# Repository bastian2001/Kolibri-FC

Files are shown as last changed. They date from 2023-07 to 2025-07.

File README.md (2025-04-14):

# RP2350 Flight Controller for FPV

I wanted to have some fun designing my own flight controller in both hardware and software. [This project of mine](https://github.com/bastian2001/Hardware-DShot-on-RP2040) ([superseded](https://github.com/bastian2001/pico-bidir-dshot/)) served as a proof of concept (and mostly minimal example) that the RP2040 is capable of driving DShot through the PIO (Programmable IO) hardware.

The PCB is in its fifth testing revision, which includes (hardware features):

-   3-8S input voltage
-   5V 2.5A, 10V 2.5A buck converters
-   30.5mm stack mounting
-   BMI270
-   Analog character based OSD similar to Betaflight/iNav
-   SD card slot for blackbox, now with SDIO
-   Barometer (STM LPS22HB)
-   Gemini 2.4GHz ELRS receiver with 4 additional PWM outputs
-   Speaker driver up to VBat

Main software features:

-   Configurator
-   Acro and angle modes
-   altitude and position hold modes (working, but need to be tuned)
-   ELRS
-   GPS (UBlox) and Compass (HMC5883 + QMC5883L)
-   Bidirectional DShot 4800 (tested up to 1200)
-   Variable frequency beeper with WAV support
-   SD-Blackbox incl. viewer
-   Barometer (Goertek SPL06-001 + STM LPS22HB)

Future shit:

-   return to home and waypoint mission (incl. emergency switch)
-   3D camera dolly
-   trick trainer, that does a trick for you and displays in the OSD how good or bad you were at repeating that trick

Practically speaking, is there any reason to choose this over Betaflight or iNav? Likely not, but I want to have a challenge.

## Configurator screenshots

Home Page with a general preview of the quad's orientation, some status info and general controls
grafik

Blackbox viewer integrated into the configurator, you can record ELRS data, setpoints, rotation, attitude, PIDs, GPS, RPM, magnetometer and much more. Size is practically unlimited (SD card logging), but 1MB is about 10 seconds when logging practically everything. Integrated filtering to smooth noisy data, multiple graphs and multiple traces per graph, JSON converter for external analysis, pinch to zoom (touchscreen support). Don't mind the "Start Time" - it's wrong. The blackbox got some updates, which changed the interpretation of the timestamp.
grafik

Tasks viewer shows the execution duration and frequency of all the tasks to check they're running fast enough and to aid optimization of code (counting of frequency, max, min and average durations are not always done the same, so the results need to be checked against the code to see how each task is counted)
grafik

Receiver page shows status of the RX and each channel
grafik

Tuning is limited to basic PIDs and rates for now - filters have hardcoded cutoffs 😅
grafik

GPS + Mag page shows X/Y Y/Z and Z/X graphs of the magnetometer to check calibration and skew. Lower side shows data obtained by the GPS (no GPS fix right now, so time is off)
grafik

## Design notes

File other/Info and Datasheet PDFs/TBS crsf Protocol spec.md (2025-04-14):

Copied from https://github.com/tbs-fpv/tbs-crsf-spec/blob/main/crsf.md

CRSF V3 Protocol Specification © 2020 by TBS Avionics Co LTD is licensed under Creative Commons Attribution-ShareAlike 4.0 International

Unmodified, access date is April 14th 2025.

# CRSF Protocol

# Table of Contents

-   [CRSF Protocol](#crsf-protocol)
-   [Table of Contents](#table-of-contents)
-   [Features](#features)
-   [Purpose](#purpose)
-   [Acronyms](#acronyms)
-   [Hardware](#hardware)
    -   [Single-Wire Half-Duplex UART](#single-wire-half-duplex-uart)
    -   [Dual-Wire Full-Duplex UART](#dual-wire-full-duplex-uart)
    -   [Multi-master I2C (BST)](#multi-master-i2c-bst)
-   [Frame Construction](#frame-construction)
    -   [Structure](#structure)
    -   [Broadcast Frame](#broadcast-frame)
    -   [Extended Header Frame](#extended-header-frame)
    -   [Frame Details](#frame-details)
-   [Routing](#routing)
-   [CRC](#crc)
-   [Device Addresses](#device-addresses)
-   [Broadcast Frame Types](#broadcast-frame-types)
    -   [0x02 GPS](#0x02-gps)
    -   [0x03 GPS Time](#0x03-gps-time)
    -   [0x06 GPS Extended](#0x06-gps-extended)
    -   [0x07 Variometer Sensor](#0x07-variometer-sensor)
    -   [0x08 Battery Sensor](#0x08-battery-sensor)
    -   [0x09 Barometric Altitude & Vertical Speed](#0x09-barometric-altitude--vertical-speed)
    -   [0x0A Airspeed](#0x0a-airspeed)
    -   [0x0B Heartbeat](#0x0b-heartbeat)
    -   [0x0C RPM](#0x0C-rpm)
    -   [0x0D TEMP](#0x0D-temp)
    -   [0x0F Discontinued](#0x0f-discontinued)
    -   [0x10 VTX Telemetry](#0x10-vtx-telemetry)
    -   [0x14 Link Statistics](#0x14-link-statistics)
    -   [0x16 RC Channels Packed Payload](#0x16-rc-channels-packed-payload)
    -   [0x17 Subset RC Channels Packed](#0x17-subset-rc-channels-packed)
    -   [0x18 RC Channels Packed 11-bits (Unused)](#0x18-rc-channels-packed-11-bits-unused)
    -   [0x19 - 0x1B Reserved Crossfire](#0x19---0x1b-reserved-crossfire)
    -   [0x1C Link Statistics RX](#0x1c-link-statistics-rx)
    -   [0x1D Link Statistics TX](#0x1d-link-statistics-tx)
    -   [0x1E Attitude](#0x1e-attitude)
    -   [0x1F MAVLink FC](#0x1f-mavlink-fc)
    -   [0x21 Flight Mode](#0x21-flight-mode)
    -   [0x22 ESP_NOW Messages](#0x22-esp_now-messages)
    -   [0x27 Reserved](#0x27-reserved)
-   [Extended Frame Types](#extended-frame-types)
    -   [0x28 Parameter Ping Devices](#0x28-parameter-ping-devices)
    -   [0x29 Parameter Device Information](#0x29-parameter-device-information)
    -   [Chunks](#chunks)
    -   [0x2B Parameter Settings (Entry)](#0x2b-parameter-settings-entry)
        -   [Parameter Type Definitions & Hidden Bit](#parameter-type-definitions--hidden-bit)
        -   [OUT_OF_RANGE](#out_of_range)
        -   [UINT8, INT8, UINT16, INT16, UINT32, INT32](#uint8-int8-uint16-int16-uint32-int32)
        -   [FLOAT](#float)
        -   [TEXT_SELECTION](#text_selection)
        -   [STRING](#string)
        -   [FOLDER](#folder)
        -   [INFO](#info)
        -   [COMMAND](#command)
    -   [0x2C Parameter Settings (Read)](#0x2c-parameter-settings-read)
    -   [0x2D Parameter Value (Write)](#0x2d-parameter-value-write)
    -   [0x32 Direct Commands](#0x32-direct-commands)
        -   [0x32.0xFF Command ACK](#0x320xff-command-ack)
        -   [0x32.0x01 FC Commands](#0x320x01-fc-commands)
        -   [0x32.0x03 Bluetooth Command](#0x320x03-bluetooth-command)
        -   [0x32.0x05 OSD Commands](#0x320x05-osd-commands)
        -   [0x32.0x08 VTX Commands](#0x320x08-vtx-commands)
        -   [0x32.0x09 LED](#0x320x09-led)
        -   [0x32.0x0A General](#0x320x0a-general)
        -   [0x32.0x10 Crossfire](#0x320x10-crossfire)
        -   [0x32.0x12 Reserved](#0x320x12-reserved)
        -   [0x32.0x20 Flow Control Frame](#0x320x20-flow-control-frame)
        -   [0x32.0x22 Screen Command](#0x320x22-screen-command)
            -   [0x32.0x22.0x01 Pop-up Message Start](#0x320x220x01-pop-up-message-start)
            -   [0x32.0x22.0x02 Selection Return Value](#0x320x220x02-selection-return-value)
            -   [0x32.0x22.0x03 Reserved](#0x320x220x03-reserved)
            -   [0x32.0x22.0x04 Reserved](#0x320x220x04-reserved)
    -   [0x34 Logging](#0x34-logging)
    -   [0x36 Reserved](#0x36-reserved)
    -   [0x38 Reserved](#0x38-reserved)
    -   [0x3A - Remote Related Frames](#0x3a---remote-related-frames)
        -   [0x3A.0x01 - 0x3A.0x09 - Reserved](#0x3a0x01---0x3a0x09---reserved)
        -   [0x3A.0x10 Timing Correction (CRSF Shot)](#0x3a0x10-timing-correction-crsf-shot)
    -   [0x3C Game](#0x3c-game)
    -   [0x3E Reserved](#0x3e-reserved)
    -   [0x40 Reserved](#0x40-reserved)
    -   [0x78 - 0x79 KISSFC Reserved](#0x78---0x79-kissfc-reserved)
    -   [0x7A MSP Request / 0x7B Response](#0x7a-msp-request--0x7b-response)
    -   [0x7F ArduPilot Legacy Reserved](#0x7f-ardupilot-legacy-reserved)
    -   [0x80 ArduPilot Reserved Passthrough Frame](#0x80-ardupilot-reserved-passthrough-frame)
    -   [0x81, 0x82 mLRS Reserved](#0x81-0x82-mlrs-reserved)
    -   [0xAA CRSF MAVLink Envelope](#0xaa-crsf-mavlink-envelope)
    -   [0xAC CRSF MAVLink System Status Sensor](#0xac-crsf-mavlink-system-status-sensor)
-   [End of Document](#end-of-document)

# Features

-   Low latency high update rate for RC signals between RC - TX and RX - FC
-   Bidirectional communication
-   Share telemetry from flying platform to the RC
-   Edit configuration for direct connected devices and remotely connected devices (RC can configure FC or OSD over CRSF)
-   Share receiver serial number to TX, so it can be matched to model memory.

# Purpose

This document serves as a public "single source of truth", maintained by TBS, documenting the protocol. It serves as reference for implementation of CRSF-compatible devices, as well as allows developers not associated with TBS to voice requirements and suggest extensions to the existing protocols. It will further establish CRSF as the most widely implemented modern communication protocol for R/C devices.

# Acronyms

-   **CRSF** Binary frame-based protocol for radio-controlled devices. The subject of this document.
-   **RC** Remote Controller. The pilot control input device.
-   **TX** Transmitter (which is actually a transceiver). Usually a part (external or embedded as a radio module) of RC.
-   **RX** Receiver (which is also a transceiver). Might be as a separate device or embedded with FC or VTX.
-   **FC** Flight Controller.
-   **VTX** Video Transmitter.
-   **VRX** Video Receiver.

# Hardware

## Single-Wire Half-Duplex UART

This configuration is usually used between RC and TX. The RC acts as master in this case and TX responds with telemetry if it’s synchronized to the RC frames sent by the RC. The RC must send only one frame with pre-configured or negotiated frequency and must switch the line into the high-impedance mode and wait for a response from TX.

The UART by default runs at **400 kbaud 8N1** (inverted or non-inverted) at **3.3V** level, but it also supports 115.2 kbaud, and higher (1Mbaud, 2Mbaud) depending on hardware (see [0x70 CRSF Protocol Speed Proposal](#0x320x0a-general)). It is recommended that TX modules are configured to the same baud rate, or that they latch on to the correct baudrate automatically. The maximum frame-rate must be chosen depending on the baudrate for be able for RC and TX send frames with maximum length (64 bytes) in one frame.

## Dual-Wire Full-Duplex UART

This configuration is usually used on the flying platform side. Two devices are connected by regular UART connection. Only non-inverted (regular) UART is supported in this configuration. The UART runs by default at **416666 baud 8N1 at 3.0 to 3.3V level**, but baudrate can be negotiated to be higher to facilitate faster transmission for reducing latency.

## Multi-master I2C (BST)

(EOL) BST is a multi master I2C bus. It runs at 3.3V level at 100kHz using 7 bit addresses. Device addresses already contain the R/W bit. Which means the list is each device’s write address and read address is Device addresses + 1. Each device supporting BST should release SDA in any case to not block the bus. It’s recommended to monitor the heartbeat message and reset the interface if there is a timeout of 1.5s. It’s required to support general call frames which will be called broadcast frames within this document.

# Frame Construction

## Structure

The basic structure for each frame is the same. There is a range of Types with an extended header which will have the first few bytes of payload standardized. This is required to route frame across multiple devices for point to point communication. Each CRSF frame is not longer than **64 bytes** (including the Sync and CRC bytes)

## Broadcast Frame

```mermaid
flowchart LR
    id0[Sync byte] ~~~ id1[Frame Length] ~~~ Type ~~~ Payload ~~~ CRC
```

## Extended Header Frame

```mermaid
flowchart LR
    id0[Sync byte] ~~~ id1[Frame Length] ~~~ Type~~~ id2[Destination Address]  ~~~ id3[Origin Address]  ~~~ Payload ~~~ CRC
```

## Frame Details

-   **Sync byte** might be one of (so, receiving device should expect any of):
    -   Serial sync byte: **0xC8**;
    -   Broadcast device address: **0x00**;
    -   Device address (see addresses below).
-   **Frame length:** number of bytes in the frame excluding Sync byte and Frame Length (basically, entire frame size -2)
    -   **Broadcast Frame:** Type + Payload + CRC
    -   **Extended header frame:** Type + Destination address + Origin address + Payload + CRC
    -   Valid range is between 2 and 62. If this uint8 value is out of valid range the frame must be discarded.
-   **Type:** Frame type
-   **Endianness:** Big endian (MSB)

Frame size may be bigger than expected frame of given type. This should not be a reason to count the frame invalid. Frame receiver should just ignore extra fields. It's possible that frame sender supports a newer CRSF protocol version and sends some additional fields after known ones.

And vice-versa: if a frame has some optional fields, sometimes this fields might be set as empty fields (e.g. zero-length null-terminated string) but sometimes those fields might be absent and the frame size shortened. Don't try to read optional fields beyond frame payload.

# Routing

If a device has more than one CRSF port it’s required to forward all received frames to the other ports. CRSF works as a star network with fixed address tables on each node. It’s forbidden to use any loop connection as it would keep forwarding the same message endlessly.

# CRC

CRC includes Type and Payload of each frame (doesn't include sync byte and frame length).

CRC8 implementation with polynom = x7+ x6+ x4+ x2+ x0 (0xD5)

code example:

```cpp
unsigned char crc8tab[256] = {
    0x00, 0xD5, 0x7F, 0xAA, 0xFE, 0x2B, 0x81, 0x54, 0x29, 0xFC, 0x56, 0x83, 0xD7, 0x02, 0xA8, 0x7D,
    0x52, 0x87, 0x2D, 0xF8, 0xAC, 0x79, 0xD3, 0x06, 0x7B, 0xAE, 0x04, 0xD1, 0x85, 0x50, 0xFA, 0x2F,
    0xA4, 0x71, 0xDB, 0x0E, 0x5A, 0x8F, 0x25, 0xF0, 0x8D, 0x58, 0xF2, 0x27, 0x73, 0xA6, 0x0C, 0xD9,
    0xF6, 0x23, 0x89, 0x5C, 0x08, 0xDD, 0x77, 0xA2, 0xDF, 0x0A, 0xA0, 0x75, 0x21, 0xF4, 0x5E, 0x8B,
    0x9D, 0x48, 0xE2, 0x37, 0x63, 0xB6, 0x1C, 0xC9, 0xB4, 0x61, 0xCB, 0x1E, 0x4A, 0x9F, 0x35, 0xE0,
    0xCF, 0x1A, 0xB0, 0x65, 0x31, 0xE4, 0x4E, 0x9B, 0xE6, 0x33, 0x99, 0x4C, 0x18, 0xCD, 0x67, 0xB2,
    0x39, 0xEC, 0x46, 0x93, 0xC7, 0x12, 0xB8, 0x6D, 0x10, 0xC5, 0x6F, 0xBA, 0xEE, 0x3B, 0x91, 0x44,
    0x6B, 0xBE, 0x14, 0xC1, 0x95, 0x40, 0xEA, 0x3F, 0x42, 0x97, 0x3D, 0xE8, 0xBC, 0x69, 0xC3, 0x16,
    0xEF, 0x3A, 0x90, 0x45, 0x11, 0xC4, 0x6E, 0xBB, 0xC6, 0x13, 0xB9, 0x6C, 0x38, 0xED, 0x47, 0x92,
    0xBD, 0x68, 0xC2, 0x17, 0x43, 0x96, 0x3C, 0xE9, 0x94, 0x41, 0xEB, 0x3E, 0x6A, 0xBF, 0x15, 0xC0,
    0x4B, 0x9E, 0x34, 0xE1, 0xB5, 0x60, 0xCA, 0x1F, 0x62, 0xB7, 0x1D, 0xC8, 0x9C, 0x49, 0xE3, 0x36,
    0x19, 0xCC, 0x66, 0xB3, 0xE7, 0x32, 0x98, 0x4D, 0x30, 0xE5, 0x4F, 0x9A, 0xCE, 0x1B, 0xB1, 0x64,
    0x72, 0xA7, 0x0D, 0xD8, 0x8C, 0x59, 0xF3, 0x26, 0x5B, 0x8E, 0x24, 0xF1, 0xA5, 0x70, 0xDA, 0x0F,
    0x20, 0xF5, 0x5F, 0x8A, 0xDE, 0x0B, 0xA1, 0x74, 0x09, 0xDC, 0x76, 0xA3, 0xF7, 0x22, 0x88, 0x5D,
    0xD6, 0x03, 0xA9, 0x7C, 0x28, 0xFD, 0x57, 0x82, 0xFF, 0x2A, 0x80, 0x55, 0x01, 0xD4, 0x7E, 0xAB,
    0x84, 0x51, 0xFB, 0x2E, 0x7A, 0xAF, 0x05, 0xD0, 0xAD, 0x78, 0xD2, 0x07, 0x53, 0x86, 0x2C, 0xF9};

uint8_t crc8(const uint8_t * ptr, uint8_t len)
{
    uint8_t crc = 0;
    for (uint8_t i=0; i<len; i++)
        crc = crc8tab[crc ^ *ptr++];
    return crc;
}
```

# Device Addresses

-   **0x00** Broadcast address
-   **0x0E** Cloud
-   **0x10** USB Device
-   **0x12** Bluetooth Module/WiFi
-   **0x13** Wi-Fi receiver (mobile game/simulator)
-   **0x14** Video Receiver
-   _0x20-0x7F Dynamic address space for NAT_
-   **0x80** OSD / TBS CORE PNP PRO
-   **0x90** ESC 1
-   **0x91** ESC 2
-   **0x92** ESC 3
-   **0x93** ESC 4
-   **0x94** ESC 5
-   **0x95** ESC 6
-   **0x96** ESC 7
-   **0x97** ESC 8
-   _0x8A Reserved_
-   _0xB0 Crossfire reserved_
-   _0xB2 Crossfire reserved_
-   **0xC0** Voltage/ Current Sensor / PNP PRO digital current sensor
-   **0xC2** GPS / PNP PRO GPS
-   **0xC4** TBS Blackbox
-   **0xC8** Flight controller
-   _0xCA Reserved_
-   **0xCC** Race tag
-   **0xCE** VTX
-   **0xEA** Remote Control
-   **0xEC** R/C Receiver / Crossfire Rx
-   **0xEE** R/C Transmitter Module / Crossfire Tx
-   _0xF0 reserved_
-   _0xF2 reserved_

# Broadcast Frame Types

Frames with type lower than 0x27 are broadcast frames and have simple (short) header.

## 0x02 GPS

```cpp
    int32_t latitude;       // degree / 10`000`000
    int32_t longitude;      // degree / 10`000`000
    uint16_t groundspeed;   // km/h / 100
    uint16_t heading;       // degree / 100
    uint16_t altitude;      // meter - 1000m offset
    uint8_t satellites;     // # of sats in view
```

## 0x03 GPS Time

This frame is needed for synchronization with the ublox time pulse. The maximum offset of time is +/-10ms.

```cpp
    int16_t year;
    uint8_t month;
    uint8_t day;
    uint8_t hour;
    uint8_t minute;
    uint8_t second;
    uint16_t millisecond;
```

## 0x06 GPS Extended

```cpp
    uint8_t fix_type;       // Current GPS fix quality
    int16_t n_speed;        // Northward (north = positive) Speed [cm/sec]
    int16_t e_speed;        // Eastward (east = positive) Speed [cm/sec]
    int16_t v_speed;        // Vertical (up = positive) Speed [cm/sec]
    int16_t h_speed_acc;    // Horizontal Speed accuracy cm/sec
    int16_t track_acc;      // Heading accuracy in degrees scaled with 1e-1 degrees times 10)
    int16_t alt_ellipsoid;  // Meters Height above GPS Ellipsoid (not MSL)
    int16_t h_acc;          // horizontal accuracy in cm
    int16_t v_acc;          // vertical accuracy in cm
    uint8_t reserved;
    uint8_t hDOP;           // Horizontal dilution of precision,Dimensionless in nits of.1.
    uint8_t vDOP;           // vertical dilution of precision, Dimensionless in nits of .1.
```

## 0x07 Variometer Sensor

```cpp
    int16_t v_speed;        // Vertical speed cm/s
```

## 0x08 Battery Sensor

```cpp
    int16_t voltage;        // Voltage (LSB = 10 µV)
    int16_t current;        // Current (LSB = 10 µA)
    uint24_t capacity_used; // Capacity used (mAh)
    uint8_t remaining;      // Battery remaining (percent)
```

## 0x09 Barometric Altitude & Vertical Speed

These frame allows sending altitude and vertical speed in a bit-efficient way. It allows in 3 bytes combine dm-precision altitude with 32-km range and 3cm/s-precision vertical speed with 25m/s range.

```cpp
    uint16_t altitude_packed;       // Altitude above start (calibration) point
                                    // See description below.
    int8_t   vertical_speed_packed; // vertical speed. See description below.
```

Altitude value depends on MSB (bit 15):

-   MSB = 0: altitude is in decimeters - 10000dm offset (so 0 represents -1000m; 10000 represents 0m (starting altitude); 0x7fff represents 2276.7m);
-   MSB = 1: altitude is in meters. Without any offset.

altitude pack/unpack functions example:

```cpp
int32_t get_altitude_dm(uint16_t packed){
    return (packed & 0x8000) ? (packed & 0x7fff) * 10 : (packed - 10000);
}

// Due to OpenTX counts any 0xFFFF value as incorrect,
// the maximum sending value is limited to 0xFFFE (32766 meters)
//pack function example:
uint16_t get_altitude_packed (int32_t altitude_dm){
    enum
    {
        ALT_MIN_DM = 10000,                     //minimum altitude in dm
        ALT_THRESHOLD_DM = 0x8000 - ALT_MIN_DM, //altitude of precision
                                                // changing in dm
        ALT_MAX_DM = 0x7ffe * 10 - 5,           //maximum altitude in dm
    }

    if(altitude_dm < -ALT_MIN_DM)               //less than minimum altitude
        return 0;                               //minimum
    if(altitude_dm > ALT_MAX_DM)                //more than maximum
        return 0xfffe;                          //maximum
    if(altitude_dm < ALT_THRESHOLD_DM)          //dm-resolution range
        return altitude_dm + ALT_MIN_DM;
    return ((altitude_dm + 5) / 10) | 0x8000;   //meter-resolution range
}
```

vertical speed is represented in cm/s with logarithmic scale and (un)packed by functions:

```cpp
const int   Kl = 100;       // linearity constant;
const float Kr = .026;      // range constant;

int8_t  get_vertical_speed_packed (int16 vertical_speed_cm_s){
    return (int8_t)(log(abs(vertical_speed_cm_s)/Kl + 1)/Kr)
                                 * sign(vertical_speed_cm_s);
}

int16_t get_vertical_speed_cm_s (int8_t vertical_speed_packed){
    return exp(abs(vertical_speed_packed * Kr) - 1) * Kl
                           * sign(vertical_speed_packed);
}

```

Such constants give ±2500cm/s range and 3cm/s precision at low speeds and 70cm/s precision at speed about 25m/s;

## 0x0A Airspeed

```cpp
    uint16_t speed;             // Airspeed in 0.1 * km/h (hectometers/h)
```

## 0x0B Heartbeat

```cpp
    int16_t origin_address;             // Origin Device address
```

## 0x0C RPM

Frame type used to transmit RPM (revolutions per minute) telemetry data from the craft to the transmitter. This frame can be used to report motor or propeller RPM for monitoring performance or diagnostics.

```cpp
    uint8_t    rpm_source_id;  // Identifies the source of the RPM data (e.g., 0 = Motor 1, 1 = Motor 2, etc.)
    int24_t    rpm_value[];      // 1 - 19 RPM values with negative ones representing the motor spinning in reverse
```

## 0x0D TEMP

Frame type used to transmit temperature telemetry data from the vehicle to the transmitter. This frame can be used to report temperature readings from various sources on the vehicle, such as motors, ESCs, or the environment.

```cpp
    uint8_t     temp_source_id;     // Identifies the source of the temperature data (e.g., 0 = FC including all ESCs, 1 = Ambient, etc.)
    int16_t     temperature[];        // up to 20 temperature values in deci-degree (tenths of a degree) Celsius (e.g., 250 = 25.0°C, -50 = -5.0°C)
```

## 0x0F Discontinued

## 0x10 VTX Telemetry

```cpp
    uint8_t     origin_address;
    uint8_t     power_dBm;          // VTX power in dBm
    uint16_t    frequency_MHz;      // VTX frequency in MHz
    uint8_t     pit_mode:1;         // 0=Off, 1=On
    uint8_t     pitmode_control:2;  // 0=Off, 1=On, 2=Switch, 3=Failsafe
    uint8_t     pitmode_switch:4;   // 0=Ch5, 1=Ch5 Inv, … , 15=Ch12 Inv
```

## 0x14 Link Statistics

Uplink is the connection from the ground to the UAV and downlink the opposite direction

```cpp
    uint8_t     up_rssi_ant1;       // Uplink RSSI Antenna 1 (dBm * -1)
    uint8_t     up_rssi_ant2;       // Uplink RSSI Antenna 2 (dBm * -1)
    uint8_t     up_link_quality;    // Uplink Package success rate / Link quality (%)
    int8_t      up_snr;             // Uplink SNR (dB)
    uint8_t     active_antenna;     // number of currently best antenna
    uint8_t     rf_profile;         // enum {4fps = 0 , 50fps, 150fps}
    uint8_t     up_rf_power;        // enum {0mW = 0, 10mW, 25mW, 100mW,
                                    // 500mW, 1000mW, 2000mW, 250mW, 50mW}
    uint8_t     down_rssi;          // Downlink RSSI (dBm * -1)
    uint8_t     down_link_quality;  // Downlink Package success rate / Link quality (%)
    int8_t      down_snr;           // Downlink SNR (dB)
```

## 0x16 RC Channels Packed Payload

16 channels packed into 22 bytes. In case of a Failsafe, this frame will no longer be sent (when the failsafe type is set to "cut"). It is recommended to wait for 1 second before starting the FC failsafe routine.

```cpp
#define TICKS_TO_US(x)  ((x - 992) * 5 / 8 + 1500)
#define US_TO_TICKS(x)  ((x - 1500) * 8 / 5 + 992)

// Center (1500µs) = 992

struct
{
    int channel_01: 11;
    int channel_02: 11;
    int channel_03: 11;
    int channel_04: 11;
    int channel_05: 11;
    int channel_06: 11;
    int channel_07: 11;
    int channel_08: 11;
    int channel_09: 11;
    int channel_10: 11;
    int channel_11: 11;
    int channel_12: 11;
    int channel_13: 11;
    int channel_14: 11;
    int channel_15: 11;
    int channel_16: 11;
};
```

## 0x17 Subset RC Channels Packed

> [!WARNING]
> This frame is discouraged for implementation. Revision is in progress.

```cpp
// Calculation example to convert rc values to channel values
#define PACK_TX(x)          ((x - 3750) * 8 / 25 + 993)
#define UNPACK_RX(x, S)     (x * S + 988)
// S = 1.0 for 10-bit, S = 0.5 for 11-bit, S = 0.25 for 12-bit, S = 0.125 for 13-bit

struct PACKED
{
    uint8_t     starting_channel:5;             // which channel number is the first one in the frame
    uint8_t     res_configuration:2;            // configuration for the RC data resolution
                                                // (10 - 13 bits)
    uint8_t     digital_switch_flag:1;          // configuration bit for digital channel
    uint16_t    channel[]:resolution;           // variable amount of channels
                                                // (with variable resolution based on the
                                                // res_configuration)
                                                // based on the frame size
    uint16_t    digital_switch_channel[]:10;    // digital switch channel
};
```

## 0x18 RC Channels Packed 11-bits (Unused)

same as 0x16, but same conversion style as 0x17

## 0x19 - 0x1B Reserved Crossfire

## 0x1C Link Statistics RX

```cpp
    uint8_t rssi_db;        // RSSI (dBm * -1)
    uint8_t rssi_percent;   // RSSI in percent
    uint8_t link_quality;   // Package success rate / Link quality (%)
    int8_t  snr;            // SNR (dB)
    uint8_t rf_power_db;    // rf power in dBm
```

## 0x1D Link Statistics TX

```cpp
    uint8_t rssi_db;        // RSSI (dBm * -1)
    uint8_t rssi_percent;   // RSSI in percent
    uint8_t link_quality;   // Package success rate / Link quality (%)
    int8_t  snr;            // SNR (dB)
    uint8_t rf_power_db;    // rf power in dBm
    uint8_t fps;            // rf frames per second (fps / 10)
```

## 0x1E Attitude

> [!WARNING]
> Angle values must be in -180° +180° range!

```cpp
    int16_t pitch;  // Pitch angle (LSB = 100 µrad)
    int16_t roll;   // Roll angle  (LSB = 100 µrad)
    int16_t yaw;    // Yaw angle   (LSB = 100 µrad)
```

## 0x1F MAVLink FC

```cpp
    int16_t     airspeed;
    uint8_t     base_mode;      // vehicle mode flags, defined in MAV_MODE_FLAG enum
    uint32_t    custom_mode;    // autopilot-specific flags
    uint8_t     autopilot_type; // FC type; defined in MAV_AUTOPILOT enum
    uint8_t     firmware_type;  // vehicle type; defined in MAV_TYPE enum
```

**Official MAVLink Documentation:**

-   [MAV_MODE_FLAG enum](https://mavlink.io/en/messages/common.html#MAV_MODE_FLAG)
-   [MAV_AUTOPILOT enum](https://mavlink.io/en/messages/common.html#MAV_AUTOPILOT)
-   [MAV_TYPE enum](https://mavlink.io/en/messages/common.html#MAV_TYPE)

## 0x21 Flight Mode

```cpp
    char[]  Flight mode  // Null-terminated string
```

## 0x22 ESP_NOW Messages

```cpp
    uint8_t VAL1;           // Used for Seat Position of the Pilot
    uint8_t VAL2;           // Used for the Current Pilots Lap
    char    VAL3[15];       // 15 characters for the lap time current/split
    char    VAL4[15];       // 15 characters for the lap time current/split
    char    FREE_TEXT[20];  // Free text of 20 character at the bottom of the screen
```

## 0x27 Reserved

# Extended Frame Types

Frames with type 0x28 and higher (except explicitly mentioned) have extended header (with destination and origin).

## 0x28 Parameter Ping Devices

The host can ping a specific device (destination node address of device) or all devices (destination node address 0x00 Broadcast address) and they will answer with the [Parameter device information frame](#0x29-parameter-device-information). The frame has no payload.

## 0x29 Parameter Device Information

```cpp
    char[]      Device_name;        // Null-terminated string
    uint32_t    Serial_number;
    uint32_t    Hardware_ID;
    uint32_t    Firmware_ID;
    uint8_t     Parameters_total;   // Total amount of parameters
    uint8_t     Parameter_version_number;
```

## Chunks

Maximum CRSF frame size is 64 bytes (including sync byte and CRC). The host should always read ([0x2C Parameter settings (read)](#0x2c-parameter-settings-read)) chunk number 0 by default. If the read parameter ([0x2B Parameter settings (entry)](#0x2b-parameter-settings-entry)) fits the maximum size it will answer with chunks remaining 0 inside the parameter frame. Otherwise, it will send how many chunks are left to read.

**Example of Parameter settings frames (0x2B and 0x2C) chain:**

```mermaid
---
title: Example
---
sequenceDiagram

    Host->>Device: (0x2C) Request: Read Param 2, Chunk 0
    Device->>Host: (0x2B) Reply: Param 2, Chunks remaining : 2
    note over Host,Device: parameter is too big to fit 62 bytes.The device split<br/>it up in 3 chunks. First chunk is sent with this frame<br/>and 2 are remaining

    Host->>Device: (0x2C) Request: Read Param 2, Chunk 1
    Device->>Host: (0x2B) Reply: Param 2, Chunks remaining: 1
    note over Host,Device: as the device answered with a chunk size >0,<br/>the host keeps reading the same parameter<br/>and increases the chunk count

    Host->>Device: (0x2C) Request: Read Param 2, Chunk 2
    Device->>Host: (0x2B) Reply: Param 2, Chunks remaining: 0

    note over Host,Device: Host received last chunk so it can ready<br/>any other parameter starting over with chunk 0
    Host->>Device: (0x2C) Request: Read Param 3, Chunk 0
    Device->>Host: (0x2B) Reply: Param 3, Chunks remaining: 0
```

**Payload of chunk frames has the following structure:**

```cpp
uint8_t Parameter_number;                           // starting from 0
uint8_t Parameter_chunks_remaining;                 // Chunks remaining count
        Part of Parameter settings (entry) payload. // up to 56 bytes
```

## 0x2B Parameter Settings (Entry)

This is how a device (node address) can share a parameter to another device. See [Chunks](#chunks)

> [!NOTE]
> If Data_type_payload_chunk \<= 56 it can be sent in 1 frame, otherwise payload will be split into 2 or more frames.

```cpp
    uint8_t         Sync_byte;                  // 0xc8
    uint8_t         Frame_length;
    uint8_t         Frame_type;                 // 0x2b = Parameter settings (entry)
    uint8_t         Destination_address;        // 0xea = RC
    uint8_t         Origin_address;             // 0xee = TX
    uint8_t         Parameter_number;           // starting from 0
    uint8_t         Parameter_chunks_remaining; // Chunks remaining count
    {
        Data_type_payload_chunk;                // see payload for each type below
    }
    uint8_t         CRC_8;                      // Frame CRC (see CRC topic)
```

### Parameter Type Definitions & Hidden Bit

Parameter type is 8bit wide. The bit 7 indicates if the parameter is hidden (1 = hidden / 0 = visible). This gives the ability to dynamically show or hide parameters depending on other parameters. Bit 6-0 holds the type of parameter information (enum data_type).

```cpp
enum data_type
{
    UINT8           = 0,  // deprecated
    INT8            = 1,  // deprecated
    UINT16          = 2,  // deprecated
    INT16           = 3,  // deprecated
    UINT32          = 4,  // deprecated
    INT32           = 5,  // deprecated
    FLOAT           = 8,
    TEXT_SELECTION  = 9,
    STRING          = 10,
    FOLDER          = 11,
    INFO            = 12,
    COMMAND         = 13,
    OUT_OF_RANGE    = 127
}
```

### OUT_OF_RANGE

This type will be sent if a parameter number out of the device parameter range will be requested. It will be also sent as the last parameter to let the host know the end of the parameter list on a Parameters settings list (read request).

### UINT8, INT8, UINT16, INT16, UINT32, INT32

Suggested for deprecation. These are currently implemented via FLOAT, which is more general.

### FLOAT

Value, min, max and default are sent as an INT32. The decimal point value tells how many digits of the value are behind the decimal point. Step size is the recommended increment or decrement value to modify the value.

**Float payload**

```cpp
    uint8_t         Parent_folder;              // Parameter number of the parent folder,
                                                // 0 means root folder
    enum data_type  Data_type;                  // 0x08 = float
    char[]          Name;                       // Null-terminated string
    int32_t         Value;
    int32_t         Min;
    int32_t         Max;
    int32_t         Default;
    uint8_t         Decimal_point;
    int32_t         Step_size;
    char[]          Unit;                       // Null-terminated string
```

### TEXT_SELECTION

The value part of this entry is separated in two parts. First part is a char array with all possible values in text format. They are separated by a semicolon (;) and the array is null-terminated at the end. The second part is an uint8_t variable with the current value. The min, max and default value is represented as uint8_t number where a 0 represents the first text. To modify this parameter only the uint8_t value needs to be sent for the new value.

**Text selection payload**

```cpp
    uint8_t         Parent folder;              // Parameter number of the parent folder,
                                                // 0 means root folder
    enum data_type  Data type;                  // 0x09 = text selection
    char[]          Name;                       // Null-terminated string
    char[]          Options;                    // Null-terminated string, the string is
                                                // semicolon-delimited list of values
    uint8_t         Value;
    uint8_t         Min;
    uint8_t         Max;
    uint8_t         Default;
    char[]          Unit;                       // Null-terminated string
```

### STRING

This type is for text modification. Only the current text will be transmitted. There is no min, max and default entry sent for this type.

**String payload**

```cpp
    uint8_t         Parent_folder;              // Parameter number of the parent folder,
                                                // 0 means root folder
    enum data_type  Data_type;                  // 0x0a = string
    char[]          Name;                       // Null-terminated string
    char[]          Value;                      // Null-terminated string
    uint8_t         String_max_length;          // for string type only
```

### FOLDER

Folder is used to make a better structure of the parameters. Every parameter has a parent entry where the parameter can link to the parent folder. Additionally, the folder will provide a list of its children and append the folder name. The end of the list is marked with a 0xFF byte. The list will hold the parameter number of the children.

**Folder payload**

```cpp
    uint8_t         Parent_folder;              // Parameter number of the parent folder,
                                                // 0 means root folder
    enum data_type  Data_type;                  // 0x0b = folder
    char[]          Name;                       // Null-terminated string
    uint8_t[]       List_of_children;           // with 0xFF entry to mark the list end
```

### INFO

Value is a null terminated string. Same as STRING, except that INFO entry cannot be modified and doesn’t include maximum length.

**Info payload**

```cpp
    uint8_t         Parent_folder;              // Parameter number of the parent folder,
                                                // 0 means root folder
    enum data_type  Data_type;                  // 0x0c = info
    char[]          Name;                       // Null-terminated string
    char[]          Info;                       // Null-terminated string
```

### COMMAND

With the type command the host is able to run/execute a function on a device. This can be anything: link bind crossfire, calibrate gyro/acc, etc.

The device default state is READY. Once the host wants to execute the function it writes the parameter with status START. Depending on the function the device switches to PROGRESS, CONFIRMATION_NEEDED or READY.

When the device sends CONFIRMATION_NEEDED the host will show a confirmation box with “confirm” or “cancel” selection. If the user selects one the selection will be transmitted to the device and the function continues to execute. With the field Info the device can send additional information to the host.

If the host sends status POLL, it will force the device to send an updated status of the 0x2B Parameter settings (entry).

**Command payload**

```cpp
struct
{
    uint8_t         Parent_folder;  // Parameter number of the parent folder, 0 means root folder
    enum data_type  Data_type;      // 0x0d = command
    char[]          Name;           // Null-terminated string
    enum cmd_status Status;         // uint8_t
    uint8_t         Timeout;        // ms * 100
    char[]          Info;           // Null-terminated string
}

enum cmd_status
{
    READY               = 0, //--> feedback
    START               = 1, //<-- input
    PROGRESS            = 2, //--> feedback
    CONFIRMATION_NEEDED = 3, //--> feedback
    CONFIRM             = 4, //<-- input
    CANCEL              = 5, //<-- input
    POLL                = 6  //<-- input
}
```

**Command chain example**

```mermaid
sequenceDiagram

    Host->>Device: Read parameter (0x2C)
    Device->>Host: Send: COMMAND, Name = Bind, Status = READY, Info = NULL (0x2B)
    Host->>Device: Write: Status = START (0x2D)
    Device->>Host: Send Parameter: COMMAND, Name = Bind, Status = PROGRESS, Info = Binding (0x2B)

    Host->>Device: (optional) Status = POLL (0x2D)
    note over Host: it’s a must to send POLL from host if we wanna get the <br/>latest parameter info.For example: while getting parameter “bind”<br/>from TX (0xEE) is a must,otherwise we don’t know the RX firmware<br/>updating info
    Host->>Device: (optional) Status = POLL (0x2D)
    Host->>Device: (optional) Status = POLL (0x2D)

    note over Device: Device completed bind process
    Device->>Host: Send Parameter: COMMAND, Name = Bind, Status = READY, Info = OK (0x2B)
```

## 0x2C Parameter Settings (Read)

Request a specific parameter. This command is for re-request a parameter/chunk that didn’t make it through the link.

```cpp
    uint8_t Parameter_number;
    uint8_t Parameter_chunk_number; // Chunk number to request, starts with 0
```

## 0x2D Parameter Value (Write)

This command is for override a parameter. The destination node will answer with a [0x2B Parameter Settings (Entry)](#0x2b-parameter-settings-entry) frame sent to the origin node address for verification.

```cpp
    uint8_t Parameter_number;
            Data;               // size depending on data type
```

> [!NOTE]
> Size depending on [data type](#parameter-type-definitions-and-hidden-bit), otherwise this entry
> is not sent, f.e.:
>
> -   for TEXT_SELECTION - size 1;
> -   for FLOAT - size 4.

## 0x32 Direct Commands

Command frame

```cpp
    uint8_t     Command_ID;
    uint8_t[]   Payload;        // depending on Command ID
    uint8_t     Command_CRC8;   // 8 bit CRC POLYNOM = 0xBA
```

Command frame is protected by additional CRC at the end of its payload. The CRC includes frame type (byte 0x32), Destination, Origin, Command ID and Payload of each Command Frame.

Command_CRC8 implementation with polynom = x7+ x5+ x4+ x3+ x1 (0xBA)

> [!NOTE]
> The polynom is different from the main CRSF frame CRC.

> [!NOTE]
> Command CRC doesn't exclude CRC at the end of each CRSF frame. You will also need to include CRC at the end for the full frame

```cpp
unsigned char command_crc8tab[256] = {
    0x00, 0xBA, 0xCE, 0x74, 0x26, 0x9C, 0xE8, 0x52, 0x4C, 0xF6, 0x82, 0x38, 0x6A, 0xD0, 0xA4, 0x1E,
    0x98, 0x22, 0x56, 0xEC, 0xBE, 0x04, 0x70, 0xCA, 0xD4, 0x6E, 0x1A, 0xA0, 0xF2, 0x48, 0x3C, 0x86,
    0x8A, 0x30, 0x44, 0xFE, 0xAC, 0x16, 0x62, 0xD8, 0xC6, 0x7C, 0x08, 0xB2, 0xE0, 0x5A, 0x2E, 0x94,
    0x12, 0xA8, 0xDC, 0x66, 0x34, 0x8E, 0xFA, 0x40, 0x5E, 0xE4, 0x90, 0x2A, 0x78, 0xC2, 0xB6, 0x0C,
    0xAE, 0x14, 0x60, 0xDA, 0x88, 0x32, 0x46, 0xFC, 0xE2, 0x58, 0x2C, 0x96, 0xC4, 0x7E, 0x0A, 0xB0,
    0x36, 0x8C, 0xF8, 0x42, 0x10, 0xAA, 0xDE, 0x64, 0x7A, 0xC0, 0xB4, 0x0E, 0x5C, 0xE6, 0x92, 0x28,
    0x24, 0x9E, 0xEA, 0x50, 0x02, 0xB8, 0xCC, 0x76, 0x68, 0xD2, 0xA6, 0x1C, 0x4E, 0xF4, 0x80, 0x3A,
    0xBC, 0x06, 0x72, 0xC8, 0x9A, 0x20, 0x54, 0xEE, 0xF0, 0x4A, 0x3E, 0x84, 0xD6, 0x6C, 0x18, 0xA2,
    0xE6, 0x5C, 0x28, 0x92, 0xC0, 0x7A, 0x0E, 0xB4, 0xAA, 0x10, 0x64, 0xDE, 0x8C, 0x36, 0x42, 0xF8,
    0x7E, 0xC4, 0xB0, 0x0A, 0x58, 0xE2, 0x96, 0x2C, 0x32, 0x88, 0xFC, 0x46, 0x14, 0xAE, 0xDA, 0x60,
    0x6C, 0xD6, 0xA2, 0x18, 0x4A, 0xF0, 0x84, 0x3E, 0x20, 0x9A, 0xEE, 0x54, 0x06, 0xBC, 0xC8, 0x72,
    0xF4, 0x4E, 0x3A, 0x80, 0xD2, 0x68, 0x1C, 0xA6, 0xB8, 0x02, 0x76, 0xCC, 0x9E, 0x24, 0x50, 0xEA,
    0x48, 0xF2, 0x86, 0x3C, 0x6E, 0xD4, 0xA0, 0x1A, 0x04, 0xBE, 0xCA, 0x70, 0x22, 0x98, 0xEC, 0x56,
    0xD0, 0x6A, 0x1E, 0xA4, 0xF6, 0x4C, 0x38, 0x82, 0x9C, 0x26, 0x52, 0xE8, 0xBA, 0x00, 0x74, 0xCE,
    0xC2, 0x78, 0x0C, 0xB6, 0xE4, 0x5E, 0x2A, 0x90, 0x8E, 0x34, 0x40, 0xFA, 0xA8, 0x12, 0x66, 0xDC,
    0x5A, 0xE0, 0x94, 0x2E, 0x7C, 0xC6, 0xB2, 0x08, 0x16, 0xAC, 0xD8, 0x62, 0x30, 0x8A, 0xFE, 0x44};
```

### 0x32.0xFF Command ACK

```cpp
    uint8_t Command_ID;;
    uint8_t SubCommand_ID;
    uint8_t Action;
        // 1 mean target already take action
        // 0 mean not a correct command or no function on that command yet
    uint8_t[] or char[] Information; // null terminated string
```

### 0x32.0x01 FC Commands

```cpp
- 0x01 Force Disarm
- 0x02 Scale Channel
```

### 0x32.0x03 Bluetooth Command

```cpp
- 0x01 Reset
- 0x02 Enable
  - uint8_t Enable (0 = disable, 1 = enable)
- 0x64 Echo
```

### 0x32.0x05 OSD Commands

```cpp
- 0x01 Send Buttons:
  - uint8_t Buttons bitwise (Bit 7=Enter, 6=Up, 5=Down, 4=Left, 3=Right)
```

### 0x32.0x08 VTX Commands

```cpp
- 0x01 DISCONTINUED VTX Change Channel
  - EVO, PRO32 HV, PRO32 NANO still support this.
- 0x02 Set frequency
  - uint16_t Frequency (5000 - 6000 MHz)
- 0x03 DISCONTINUED VTX Change Power (moved to 0x08)
- 0x04 Enable PitMode on power up
  - uint8_t PitMode:1 enum (0 = OFF, 1 = ON)
  - uint8_t pitmode_control:2; (0=Off, 1=On, 2=Arm, 3=Failsafe)
  - uint8_t pitmode_switch:4; (0=Ch5, 1=Ch5 Inv, … , 15=Ch12 Inv)
- 0x05 Power up from PitMode (bare command)
- 0x06 Set Dynamic Power (15/05/2020 in EVO, PRO32 HV, PRO32 NANO)
    NOTE: Needs to be sent at 1Hz. If not received for 3s the VTX
          will revert to “0x08 Set Power” power setting
  - uint8_t Power (dBm) (0dBm can be considered as PitMode Power)
- 0x08 Set Power
  - uint8_t Power (dBm) (0dBm can be considered as PitMode Power)
```

### 0x32.0x09 LED

```cpp
- 0x01 Set to default (revert to target specific settings)
- 0x02 Override LED color (packed)
  - 9 bits H (0-359°)
  - 7 bits S (0-100%)
  - 8 bits V (0-100%)
- 0x03 Override pulse (packed)
  - uint16 duration (milliseconds from start color to stop color)
  - 9 bits H_Start (0-359°)
  - 7 bits S_Start (0-100%)
  - 8 bits V_Start (0-100%)
  - 9 bits H_Stop (0-359°)
  - 7 bits S_Stop (0-100%)
  - 8 bits V_Stop (0-100%)
- 0x04 Override blink (packed)
  - uint16 Interval
  - 9 bits H_Start (0-359°)
  - 7 bits S_Start (0-100%)
  - 8 bits V_Start (0-100%)
  - 9 bits H_Stop (0-359°)
  - 7 bits S_Stop (0-100%)
  - 8 bits V_Stop (0-100%)
- 0x05 Override shift (packed)
  - uint16 Interval
  - 9 bits H (0-359°)
  - 7 bits S (0-100%)
  - 8 bits V (0-100%)
```

### 0x32.0x0A General

```cpp
- 0x04 - 0x61 reserved
- 0x70 CRSF Protocol Speed Proposal
  - uint8_t port_id
  - uint32  proposed_baudrate
- 0x71 CRSF Protocol Speed Proposal Response
  - uint8_t port_id
  - bool    response // (1 = accepted / 0 = rejected)
```

### 0x32.0x10 Crossfire

```cpp
- 0x01 Set receiver in bind mode
- 0x02 Cancel bind mode
- 0x03 Set bind ID
- 0x05 Model selection (command to select model/receiver)
  - uint8_t Model Number
- 0x06 Current model selection (query frame of current selection)
- 0x07 Reply current model selection (reply frame of current selection)
  - uint8_t Model Number
- 0x08 reserved
- 0x09 reserved
```

### 0x32.0x12 Reserved

### 0x32.0x20 Flow Control Frame

A device can limit data rate or subscribe to a specific frame.

```cpp
- 0x01 Subscribe
  - uint8_t  Frame type
  - uint16_t Max interval time // ms
- 0x02 Unsubscribe
  - uint8_t  Frame type
```

### 0x32.0x22 Screen Command

For all device which has LCD Screen

#### 0x32.0x22.0x01 Pop-up Message Start

```cpp
    char[]  Header;                 // Null terminated string
    char[]  Info message;           // Null terminated string
    uint8_t Max_timeout_interval;   // Time in seconds
    bool    Close_button_option;
    struct                          // optional field. If its first byte is null
                                    // (selectionText is empty)
                                    // then it's only 1-byte (null) long.
    {
        char[]  selectionText;      // Null-terminated string. If empty,
                                    // then other fields don't exist.
        uint8_t value;
        uint8_t minValue;
        uint8_t maxValue;
        uint8_t defaultValue;
        char[]  unit;               // Null terminated string of measurement unit
    }       add_data;               // additional data to show (e.g. percentage).
    char[]  possible_values;        // optional field. char array with all possible response
                                    // values in text format,
                                    // they are separated by a semicolon (;) and the array
                                    // is null-terminated.
```

> [!NOTE]
> optional fields might either start with null or not even fit in the frame. Analyze frame size and don't read optional fields beyond frame payload.

#### 0x32.0x22.0x02 Selection Return Value

```cpp
    uint8_t value;
    bool    response;   // true(Process)/false(Cancel)
```

#### 0x32.0x22.0x03 Reserved

#### 0x32.0x22.0x04 Reserved

## 0x34 Logging

this frame has simple (short) header. Used for degug purpose only.

```cpp
    uint16_t logtype;
    uint32_t timestamp;
    uint32_t para1;

    ...
    uint32_t paraN;
```

## 0x36 Reserved

## 0x38 Reserved

## 0x3A - Remote Related Frames

### 0x3A.0x01 - 0x3A.0x09 - Reserved

### 0x3A.0x10 Timing Correction (CRSF Shot)

aka “RC-sync”; aka “timing correction frame” (in EdgeTX).

```cpp
    uint32_t    update_interval;    // LSB = 100ns
    int32       offset;             // LSB = 100ns, positive values = data came too early,
                                    // negative = late.
```

Despite that the values are in 100ns resolution, at least in EdgeTX it’s rounded to 1µs resolution 16-bit values right on arriving.

## 0x3C Game

```cpp
- 0x01 Add points
  - int16 amount of points
- 0x02 Command code
  - uint16 code
```

## 0x3E Reserved

## 0x40 Reserved

## 0x78 - 0x79 KISSFC Reserved

## 0x7A MSP Request / 0x7B Response

**0x7A**

-   CRSF frame which wraps MSP request **(‘$M\<’ or ‘$X\<’)**
-   Supported by Betaflight devices
-   Supported devices will respond with 0x7B

**0x7B**

-   CRSF frame which wraps MSP response **(‘$M>’,’$X>’,‘$M!’,’$X!’)**
-   Supported by Betaflight devices
-   Supported device will send this frame in response of MSP_Request (0x7A)

MSP frame over CRSF Payload packing:

-   MSP frame is stripped from header ($ + M/X + [/]/!) and CRC
-   Resulted MSP-body might be divided in chunks if it doesn't fit in one CRSF-frame.
-   A ‘Status’ byte is put before MSP-body in each CRSF-frame.
-   Status byte consists of three parts:
    -   bits 0-3 represent cyclic sequence number of the CRSF frame;
    -   bit 4 checks if current MSP chunk is the beginning (or only) of a new frame (1 if true);
    -   bits 5-6 represent the version number of MSP protocol (1 or 2 currently);
    -   bit 7 represents an error (for response only).
-   Chunk size of the MSP-body is calculated from size of CRSF frame. But size of the MSP-body must be parsed from the MSP-body itself (with respect to MSP version and Jumbo-frame).
-   The last/only CRSF-frame might be longer than needed. In such a case, the extra bytes must be ignored.
-   Maximum chunk size is defined by maximum length of CRSF frame 64 bytes, therefore, maximum MSP-chunk length is **57** bytes. Minimum chunk length might by anything, but the first chunk must consist of size and function ID (i.e., 5 bytes for MSPv2).
-   CRC of the MSP frame is not sent because it’s already protected by CRC of CRSF. If MSP CRC is needed, it should be calculated at the receiving point.
-   MSP-response must be sent to the origin of the MSP-request. It means that _[destination]_ and _[origin]_ bytes of CRSF-header in response must be the same as in request but swapped.

## 0x7F ArduPilot Legacy Reserved

## 0x80 ArduPilot Reserved Passthrough Frame

CRSF broadcast frame which wraps an ArduPilot "passthrough" packet

Passthrough packets come in three different flavours:

-   Single packet frame, used on fast links where one passthrough telemetry frame is returned for each RC frame

```cpp
      uint8_t sub_type = 0xF0;
      uint16_t appid;
      uint32_t data;
```

-   Multi-packet frame, used on slow links - packing up to 9 passthrough telemetry frames into the return from each RC frame

```cpp
      uint8_t sub_type = 0xF2;
      uint8_t size;
      struct PassthroughTelemetryPacket {
          uint16_t appid;
          uint32_t data;
      } packets[9];
```

-   Status text frame

```cpp
      uint8_t sub_type = 0xF1;
      uint8_t severity;
      char text[50];  // ( Null-terminated string )
```

## 0x81, 0x82 mLRS Reserved

The 0x80 and 0x81 broadcast frames establish the communication of mLRS TX modules with mLRS Configuration Lua scripts running on e.g. EdgeTx and OpenTx remote controllers. They encapsulate mLRS 'mBridge' protocol messages in CRSF frames. The protocol enables the setting of parameters and other functionality, but especially also communicates meta data which are needed for mLRS' parameter model, providing various information to the user, version control, and more features specific to the mLRS link system.

**0x80**: Communication from Lua script/remote controller to TX module. The frame format is:

```mermaid
flowchart LR
    0xEE ~~~ id0[Frame Length] ~~~ 0x80 ~~~ 0x4F ~~~ 0x57 ~~~ id1[Command Byte] ~~~ Payload ~~~ CRC
```

The two bytes 0x4F, 0x57 are the sync bytes of the mBridge protocol.

**0x81**: Communication from TX module to Lua script/remote controller. The frame format is:

```mermaid
flowchart LR
    0xEA ~~~ id0[Frame Length] ~~~ 0x81 ~~~ id1[Command Byte] ~~~ Payload ~~~ CRC
```

The Frame Length and CRC are as per the CRSF specification in the above. The mBridge protocol is relatively complicated, as it serves mLRS for various additional purposes besides communication with the Lua configuration script.

mLRS project home: https://github.com/olliw42/mLRS/

## 0xAA CRSF MAVLink Envelope

-   CRSF MAVLink envelope is designed to transfer MAVLink protocol over CRSF routers. It supports both MAVLink2 and MAVLink1 frames. Since MAVLink frames are generally much longer than CRSF frames (281 bytes for MAVLink2 vs 64 bytes for CRSF), MAVLink frames will be broken up into chunks.
-   Note that encoding / decoding correct chunk count while writing / reading MAVLink envelopes should be handled by the user to ensure data integrity.

```cpp
    uint8_t total_chunks  : 4;  // total count of chunks
    uint8_t current_chunk : 4;  // current chunk number
    uint8_t data_size;          // size of data (max 58)
    uint8_t data[];             // data array (58 bytes max)
```

```mermaid
---
title: Resulting CRSF frame structure
---
flowchart LR
  id0["Sync byte (0xC8)"] ~~~ id1[Frame Length] ~~~ id2["Type (0xAA)"] ~~~ id3["totalChunk(bit3 - 7) :<br/> currChunk(bit0-3)"] ~~~ id4[dataSize] ~~~ id5[dataStart ...<br/> dataEnd] ~~~ id6[CRC]
```

## 0xAC CRSF MAVLink System Status Sensor

-   CRSF frame for packing info of MAVLink enabled flight controller sensor status
-   To decode data packed within the frame, please refer to [the official wiki](https://mavlink.io/en/messages/common.html#MAV_SYS_STATUS_SENSOR)

```cpp
    uint32_t sensor_present;
    uint32_t sensor_enabled;
    uint32_t sensor_health;
```

# End of Document

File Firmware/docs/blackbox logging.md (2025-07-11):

# Blackbox

This Document describes the blackbox logging as of 11th July 2025 (version 0.0.1).

The blackbox is being logged on the SD card on the FC. Blackbox files end in .kbb, e.g. KOLI0001.kbb.
The format is binary, and the first 8 bytes are the magic sequence 0xDC 0xDF 0x4B 0x4F 0x4C 0x49 0x01 0x00, the next 3 bytes indicate the used blackbox format version (binary, e.g. 0x00 0x00 0x01 for 0.0.1).
Magic bytes have the advantage of being able to indicate (not verify) the file type. Many formats use it, e.g. images, I used this post as an inspiration for the type of magic number: https://chaos.social/@zwol@hackers.town/114155807784368727.

The file starts with a header, and then the data frames follow. Numbers of multiple bytes length are stored in Little Endian form. The header is currently 256 bytes long (including the magic number and version), with many bytes being reserved for future use. Since it is planned to store a large part of the settings in the header, this header may grow in the future.

## Header

Format: offset+length: description

-   0+8: magic number
-   8+3: version
-   11+4: UNIX timestamp of the start of the log, UTC
-   15+4: uint32 of the duration of the log in milliseconds. Initially set to 0, filled in at the end of the log. Can be used to indicate a broken log, if this is not set to a value greater than 0.
-   19+1: PID rate index, 0 = 3200Hz
-   20+1: blackbox frequency divider, e.g. 1 = 1:1 or 4 = 1:4. 0 is undefined
-   21+1: indicating the gyro ranges (0 (LSB) ... 2: gyr_range register, 3...4 acc_range register)
-   22+36: rate coefficient (fix32[3][3], 16.16 bits, first dimension is the axis: 0 = roll, 1 = pitch, 2 = yaw, second dimension is the type of coefficient: 0 = center, 1 = max, 2 = expo)
-   58+24: unused
-   82+60: PID gains (fix32[3][5], 16.16 bits, first dimension is the axis, second dimension is PID: P, I, D, FF, S)
-   142+8: enabled blackbox fields (uint64_t, bitmask, 0 = disabled, 1 = enabled)
-   150+1: motor pole count
-   rest filled with 0x00

### Blackbox Fields

Currently a 64 bit bitmask, where each bit indicates whether a field is enabled or not. The following fields are currently defined. An asterisk (\*) indicates that this field is not logged in the regular frame, but has its own frame type due to a different update frequency or other reasons. Typically, all fields are two bytes in size, any exceptions are marked with the byte size in brackets.

-   0\*: `LOG_ELRS_RAW`: Raw RC data (988-2012us) for the first 4 channels
-   1: `LOG_ROLL_SETPOINT`: 12.4 fixed int of the roll setpoint in degrees per second
-   2: `LOG_PITCH_SETPOINT`: 12.4 fixed int of the pitch setpoint in degrees per second
-   3: `LOG_THROTTLE_SETPOINT`: 12.4 fixed int of the throttle setpoint (0-2000 for 0-100% throttle)
-   4: `LOG_YAW_SETPOINT`: 12.4 fixed int of the yaw setpoint in degrees per second
-   5: `LOG_ROLL_GYRO_RAW`: 12.4 fixed int of the roll rate in degrees per second, unfiltered
-   6: `LOG_PITCH_GYRO_RAW`: 12.4 fixed int of the pitch rate in degrees per second, unfiltered
-   7: `LOG_YAW_GYRO_RAW`: 12.4 fixed int of the yaw rate in degrees per second, unfiltered
-   8: `LOG_ROLL_PID_P`: P term of the roll axis, int16
-   9: `LOG_ROLL_PID_I`: I term of the roll axis, int16
-   10: `LOG_ROLL_PID_D`: D term of the roll axis, int16
-   11: `LOG_ROLL_PID_FF`: FF term of the roll axis, int16
-   12: `LOG_ROLL_PID_S`: S term of the roll axis, int16
-   13: `LOG_PITCH_PID_P`: P term of the pitch axis, int16
-   14: `LOG_PITCH_PID_I`: I term of the pitch axis, int16
-   15: `LOG_PITCH_PID_D`: D term of the pitch axis, int16
-   16: `LOG_PITCH_PID_FF`: FF term of the pitch axis, int16
-   17: `LOG_PITCH_PID_S`: S term of the pitch axis, int16
-   18: `LOG_YAW_PID_P`: P term of the yaw axis, int16
-   19: `LOG_YAW_PID_I`: I term of the yaw axis, int16
-   20: `LOG_YAW_PID_D`: D term of the yaw axis, int16
-   21: `LOG_YAW_PID_FF`: FF term of the yaw axis, int16
-   22: `LOG_YAW_PID_S`: S term of the yaw axis, int16
-   23 (6): `LOG_MOTOR_OUTPUTS`: Quadruple of the motor outputs, each as a uint12. Can be decoded by generating a 48 bit int, and then splitting it into 4 uint12s. From LSB to MSP: RR, FR, RL, FL
-   24: `LOG_FRAMETIME`: Time in microseconds since the last recorded frame, uint16
-   25: `LOG_ALTITUDE`: 12.4 fixed int of the sensor-fused altitude, in meters, resolution is about 6cm per LSB
-   26: `LOG_VVEL`: 8.8 fixed int of the sensor-fused vertical velocity, in meters per second, resolution is about 4mm/s per LSB
-   27\*: `LOG_GPS`: Raw GPS data as supplied in the UBX-NAV-PVT message
-   28: `LOG_ATT_ROLL`: int16 of the roll angle in 0.0001 rad per LSB
-   29: `LOG_ATT_PITCH`: int16 of the pitch angle in 0.0001 rad per LSB
-   30: `LOG_ATT_YAW`: int16 of the yaw angle in 0.0001 rad per LSB, not corrected using the magnetometer, purely from the gyro
-   31 (6): `LOG_MOTOR_RPM`: Quadruple of the ERPM packets that were returned from the ESCs. Each is a 12 bit value. Use the same method as for `LOG_MOTOR_OUTPUTS` to split them. 0x000 is used to indicate that the ESC did not return a valid value. Decode it like it is a DShot telemetry packet after GCR decoding and with a stripped CRC, may include Extended DShot Telemetry data.
-   32 (6): `LOG_ACCEL_RAW`: Triple of the accelerometer raw values, each as an int16. The values directly come from the accelerometer and only have the offset calibration orientation applied, no filtering.
-   33 (6): `LOG_ACCEL_FILTERED`: Same scaling etc. as `LOG_ACCEL_RAW`, but after the low pass filter has been applied.
-   34: `LOG_VERTICAL_ACCEL`: 9.7 fixed int of the vertical acceleration in m/s²
-   35: `LOG_VVEL_SETPOINT`: 4.12 fixed int of the vertical velocity setpoint in m/s
-   36: `LOG_MAG_HEADING`: 3.13 fixed int of the magnetometer heading in rad, not filtered or interpolated using the gyro, purely from the magnetometer
-   37: `LOG_COMBINED_HEADING`: 3.13 fixed int of the combined heading in rad, filtered and interpolated using the gyro (fused sensor heading)
-   38 (4): `LOG_HVEL`: Pair of 8.8 fixed ints, each the same as `LOG_VVEL`, but for the horizontal velocity, in m/s. The first value is the north component, the second value is the east component. Fully filtered and after all sensor fusion
-   39 (3): `LOG_BARO`: Raw 24 bit pressure reading from the barometer. Interpretation depends on the barometer used
-   40 (4): `LOG_DEBUG_1`: A 32 bit debug variable
-   41 (4): `LOG_DEBUG_2`: A 32 bit debug variable
-   42: `LOG_DEBUG_3`: A 16 bit debug variable
-   43: `LOG_DEBUG_4`: A 16 bit debug variable

## Data

Each data frame starts with a frame identifier (1 byte) followed by the frame data. The following data frames exist:

-   0: `BB_FRAME_NORMAL`. The length of this frame is dictated by the enabled blackbox fields. A regular frame includes all the enabled fields, except those previously marked with an asterisk.
-   1: `BB_FRAME_FLIGHTMODE`. This frame is 1 byte long and contains the new flight mode index. This frame is stored as the first data frame after the header to indicate the flight mode at the start of the log.
-   2: `BB_FRAME_HIGHLIGHT`. This frame has no data and just indicates that the user pressed the highlight button on the transmitter. It is logged to mark a point of interest in the log.
-   3: `BB_FRAME_GPS`.This frame is logged when a GPS packet arrives. It is 92 bytes long and contains the raw UBX-NAV-PVT message, which includes the time, position, velocity, and other information. This frame (if enabled) is logged roughly 20 times per second, if the GPS receiver allows that. This frame is only stored if the GPS logging is enabled in the blackbox fields (`LOG_GPS`).
-   4: `BB_FRAME_RC`. This frame is always logged when an RC packet arrives. Since ELRS is asynchronous from the PID loop, this frame is also logged asynchronously and not part of the normal frames. The frame is 6 bytes long and stores the first 4 channels of the RC packet, each from 988-2012 as a uint12. This frame is only logged if the `LOG_ELRS_RAW` field is enabled.

These data frames are chained one after another in the file. To write a flight mode frame (with a switch to flight mode 4), then a highlight frame and then a normal frame, the file would look like this:

```
0x01 0x04 0x02 0x00 [...data for the normal frame...]
^^^^^^^^^ ^^^^ ^^^^^^^^^^^^^^^^^^^^^^^^^^^^^^^^^^^^^^
   |       |       |
   |       |       +-- normal frame (0x00 identifier + frame data)
   |       +-- highlight frame (just 0x02 identifier)
   +-- flight mode frame (0x01 identifier + flight mode index, 0x04)
```

Since the frames are generated asynchronously (dual core processor), it is uncertain (by one frame) when exactly the new flight mode applies, when exactly the highlight was pressed or when exactly the new ELRS or GPS data was first processed in the PID controller. Blackbox viewers should align the special frames to the _next_ normal frame, so that e.g. a flight mode change between frames 10 and 11 applies in frame 11.

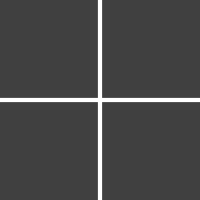
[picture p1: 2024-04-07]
Configurator/src/assets/grid.png

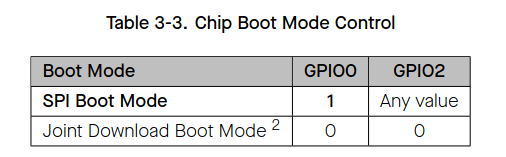
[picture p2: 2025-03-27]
PCB/PCB Version 0.5/ESP32 Boot modes.png

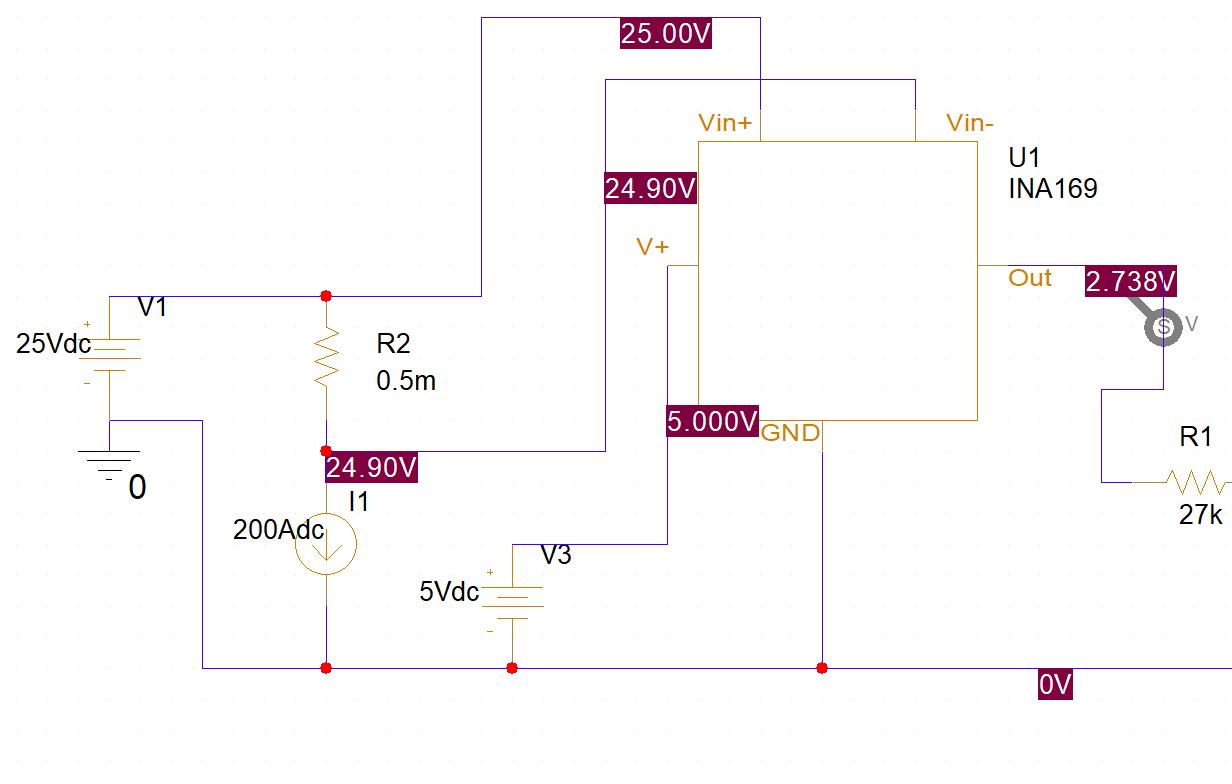
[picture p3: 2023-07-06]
other/Simulations/INA139 Current Sensor/INA139.png

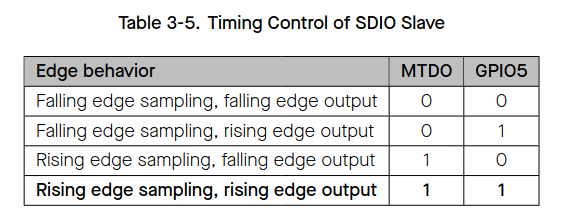
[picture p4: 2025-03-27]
PCB/PCB Version 0.5/ESP32 SDIO Strap.png

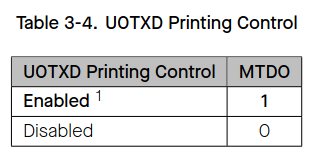
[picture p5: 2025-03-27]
PCB/PCB Version 0.5/ESP32 MTDO Strap.png

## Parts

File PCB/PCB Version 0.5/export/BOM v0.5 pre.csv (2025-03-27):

Reference | Value | LCSC # | Datasheet | Footprint | Qty | DNP
C1,C3,C4,C5,C6,C7,C8,C9,C10,C16,C17,C18,C19,C20,C21,C22,C23,C24,C25,C26,C27,C28,C33,C34,C40,C44,C45,C60,C62,C65,C67,C70,C71,C74,C76,C85,C86 | 100n | C110251 | ~ | Capacitor_SMD:C_0402_1005Metric | 37
C2,C11,C12,C13 | 4.7u | C368809 | ~ | Capacitor_SMD:C_0402_1005Metric | 4
C14,C15,C38,C39,C79,C80 | 15p | C880657 | ~ | Capacitor_SMD:C_0402_1005Metric | 6
C29,C30,C35,C50,C53,C73,C75,C81,C82,C83,C84 | 1u | 0402 + 0603 alles da | ~ | Capacitor_SMD:C_0402_1005Metric | 11
C31,C42,C43,C55,C56 | 10n | 0402 + 0603 alles da | ~ | Capacitor_SMD:C_0402_1005Metric | 6
C32,C37 | 1.5p | C76958 | ~ | Capacitor_SMD:C_0402_1005Metric | 2
C36,C77,C78 | 10u | ist da | ~ | Capacitor_SMD:C_0402_1005Metric | 3
C41,C61 | 470n | ist da | ~ | Capacitor_SMD:C_0402_1005Metric | 2
C46,C57 | 47p | ist da | ~ | Capacitor_SMD:C_0402_1005Metric | 2
C49,C54 | 220p | C7503514 | ~ | Capacitor_SMD:C_0402_1005Metric | 2
C51,C52,C58,C59 | DNF | - | ~ | Capacitor_SMD:C_0402_1005Metric | 4
C63,C64 | 1u | 0402 + 0603 alles da | ~ | Capacitor_SMD:C_0603_1608Metric | 2
C66 | 47u | ist da | ~ | Capacitor_SMD:C_1206_3216Metric | 1
C68,C69 | 2.2u | ist da | ~ | Capacitor_SMD:C_0805_2012Metric | 2
C72 | 22u | C602037 | ~ | Capacitor_SMD:C_0805_2012Metric | 1
D1,D2,D3,D4,D5,D6,D7,D8,D9,D11 | ~ | 30x C5349954 | https://www.lcsc.com/datasheet/lcsc_datasheet_2410121315_XINGLIGHT-XL-1615RGBC-WS2812B_C5349954.pdf | Kolibri custom:WS2812B_1615 | 10
D10,D12,D13 | 1N4148WS | C917117 | https://www.vishay.com/docs/85751/1n4148ws.pdf | Diode_SMD:D_SOD-323 | 3
FL1,FL2 | 2450FM07D0034T | Muss geklaut werden: C2917726, C6054595, C2651081 | https://www.mouser.co.uk/datasheet/2/611/2450FM07D0034-1375634.pdf | SamacSys_Parts:2450FM07D0034T | 2
IC1,IC3 | SX1280IMLTRT | ist da | https://datasheet.datasheetarchive.com/originals/distributors/DKDS-37/728740.pdf | SamacSys_Parts:QFN50P400X400X100-25N-D | 2
IC2,IC4 | RFX2401C | AT2401 ist da |  | SamacSys_Parts:QFN50P300X300X60-17N-D | 2
IC5,IC6 | LMR38025SDRRR | ist da | https://www.ti.com/lit/ds/symlink/lmr38025.pdf?ts=1711363220060 | SamacSys_Parts:SON50P300X300X80-13N | 2
J1 | USB_C_Receptacle_USB2.0_16P | 10x C963217 | https://www.usb.org/sites/default/files/documents/usb_type-c.zip | Kolibri custom:USB-C SMD+THT | 1
J2 | Conn_01x04_MountingPin | C2905006 | ~ | Connector_JST:JST_SH_SM04B-SRSS-TB_1x04-1MP_P1.00mm_Horizontal | 1
J3,J4 | Conn_Coaxial_Small | C5137195 | ~ | Connector_Coaxial:U.FL_Molex_MCRF_73412-0110_Vertical | 2
J5 | Conn_01x08_MountingPin | C7433429 | ~ | Connector_JST:JST_SH_SM08B-SRSS-TB_1x08-1MP_P1.00mm_Horizontal | 1
J6,J7 | Conn_01x06_MountingPin | ist da | ~ | Connector_JST:JST_SH_SM06B-SRSS-TB_1x06-1MP_P1.00mm_Horizontal | 2
J8 | Conn_01x03_MountingPin | C7433424 | ~ | Connector_JST:JST_SH_SM03B-SRSS-TB_1x03-1MP_P1.00mm_Horizontal | 1
J9 | Micro_SD_Card_Det1 | ist da | https://datasheet.lcsc.com/lcsc/2110151630_XKB-Connectivity-XKTF-015-N_C381082.pdf | Kolibri custom:Micro SD Card (TF) | 1
L1 | 3.3u | C42411119 | ~ |  | 1
L2 | 2.0n | ist da | ~ | Inductor_SMD:L_0402_1005Metric | 1
L3 | 3.0n | ist da/s.u. | ~ | Inductor_SMD:L_0402_1005Metric | 1
L4 | 24n | C401493 | ~ | Inductor_SMD:L_0402_1005Metric | 1
L5,L6 | 15u | C5344252 | ~ | Inductor_SMD:L_0402_1005Metric | 2
L7,L8 | 4.7u | C520275 | ~ | Inductor_SMD:L_Cenker_CKCS4020 | 2
P1,P2,P3,P4,P5,P6,P7,P8,P9,P10,P11,P12,P13,P14,P15,P16,P17 | ~ | - |  | Kolibri custom:Solder_Pad_rounded | 17
P18,P19,P20,P21,P22 | ~ | - |  | Kolibri custom:Solder_Pad_rounded_dual | 5
P23,P24,P25 | ~ | - |  | Kolibri custom:Solder_Pad_rect_dual | 3
P26,P27 | ~ | - |  | Kolibri custom:Solder_Pad_rect | 2
P28,P29,P30,P33,P34 | ~ | - |  | Kolibri custom:Solder_Pad_octa_dual | 5
P31,P32 | ~ | - |  | Kolibri custom:Solder_Pad_octa | 2
Q1 | BSS138 | 100x C5224263 | https://www.onsemi.com/pub/Collateral/BSS138-D.PDF | Package_TO_SOT_SMD:SOT-23 | 1
R1,R2 | 27 | 0402 + 0603 alles da | ~ | Resistor_SMD:R_0402_1005Metric | 2
R3 | 33 | C138002 | ~ | Resistor_SMD:R_0402_1005Metric | 1
R4,R21,R22,R23 | 1k | 0402 + 0603 alles da | ~ | Resistor_SMD:R_0402_1005Metric | 4
R5,R6 | 5.1k | 0402 + 0603 alles da | ~ | Resistor_SMD:R_0402_1005Metric | 2
R7,R8 | 6.8k | C2906876 | ~ | Resistor_SMD:R_0402_1005Metric | 2
R9,R10,R11,R12,R13 | 100k | 0402 ist da | ~ | Resistor_SMD:R_0402_1005Metric | 5
R14 | 39k | C328318 | ~ | Resistor_SMD:R_0402_1005Metric | 1
R15 | 40.2k | C2933097 | ~ | Resistor_SMD:R_0402_1005Metric | 1
R16,R20,R27 | 10k | 0402 + 0603 alles da | ~ | Resistor_SMD:R_0402_1005Metric | 3
R17 | 22.6k | C321379 | ~ | Resistor_SMD:R_0402_1005Metric | 1
R18 | 21.5k | 0402 ist da | ~ | Resistor_SMD:R_0402_1005Metric | 1
R19 | 90.9k | 0402 ist da | ~ | Resistor_SMD:R_0402_1005Metric | 1
R24,R25 | 75 | 0402 + 0603 alles da | ~ | Resistor_SMD:R_0402_1005Metric | 2
R26 | 120k | -> 100k | ~ | Resistor_SMD:R_0402_1005Metric | 1
S1 | Goertek SPL06-001 | -> 3x C94049 (STMicro) |  | Kolibri custom:Goertek SPL06-001 | 1
U1 | RP2350A | 10x C42411118 |  | Kolibri custom:QFN-60_EP_7x7_Pitch0.4mm | 1
U2 | BMI270 | 2x C2836813 | https://www.bosch-sensortec.com/media/boschsensortec/downloads/datasheets/bst-bmi270-ds000.pdf | Package_LGA:Bosch_LGA-14_3x2.5mm_P0.5mm | 1
U3 | ESP32-U4WDH | 2x C20622217 |  | Kolibri custom:QFN-48_EP_5x5_Pitch0.35mm | 1
U4 | TPS2116DRL | ist da | https://www.ti.com/lit/ds/symlink/tps2116.pdf | Package_TO_SOT_SMD:SOT-583-8 | 1
U5 | AT7456E | 10x C82351 |  | Package_SO:HTSSOP-28-1EP_4.4x9.7mm_P0.65mm_EP2.75x6.2mm | 1
U6 | LP5912-3.3DRV | ist da | http://www.ti.com/lit/ds/symlink/lp5912.pdf | Package_SON:WSON-6-1EP_2x2mm_P0.65mm_EP1x1.6mm_ThermalVias | 1
U7 | TPS746-3.3DRV | ist da | http://www.ti.com/lit/ds/symlink/lp5912.pdf | Package_SON:WSON-6-1EP_2x2mm_P0.65mm_EP1x1.6mm_ThermalVias | 1
U8 | WE-TVS-824015043 | ist da: C5380470 | https://www.we-online.com/components/products/datasheet/824015043.pdf | Package_TO_SOT_SMD:SOT-23-6 | 1
U9 | TLV9002S_RUG_X2QFN | ist da |  | Kolibri custom:Texas_X2QFN_RUG_10pin_1.5x2mm | 1
U10 | W25Q16JVUXIQ | 10x C2843335 | http://www.winbond.com/resource-files/w25q32jv%20revg%2003272018%20plus.pdf | Package_SON:Winbond_USON-8-1EP_3x2mm_P0.5mm_EP0.2x1.6mm | 1
Y1,Y4 | Crystal_GND24 | s.u. | ~ | Crystal:Crystal_SMD_3225-4Pin_3.2x2.5mm | 2
Y2 | Crystal_GND24 | s.u. | ~ | Crystal:Crystal_SMD_2016-4Pin_2.0x1.6mm | 1
Y3 | YXC OW7EL89CENUNFAYLC-52M | s.u. | https://www.sitime.com/support/resource-library/datasheets/sit8008-datasheet | Oscillator:Oscillator_SMD_SiT_PQFN-4Pin_2.0x1.6mm | 1
 | Crystals
 | 12MHz 2520 | C7294610
 | Abra 12MHz 3225 | C20625731
 | 27MHz 3225 von V2 | C5261177 | noch da
 | 27Mhz 2016 Test | C18214311
 | 52MHz | C3034316
 | 40MHz | C37635335
 | Murata Inductor Pi | C703121
 | Murata Coupling Cap | C77177
 | Button | C530669 | noch da

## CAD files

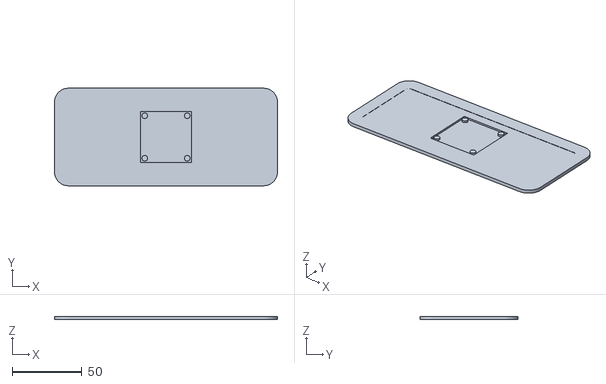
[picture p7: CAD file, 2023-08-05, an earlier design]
PCB/PCB Version 0.1/Solder rig/Alignment card.stl
160.0 x 70.0 x 2.40

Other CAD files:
PCB/PCB Version 0.1/Solder rig/Alignment card.prt

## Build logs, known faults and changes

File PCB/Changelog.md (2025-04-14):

## Design errors, fixes and improvements between PCB revisions

### V0.1

-   Known issues:
    1. Current Sensor
        - If there is no current sensor wire attached, the INA139 will output 4.3V, killing the ADC and potentially the Microcontroller
        - Solution: Wire a pullup resistor from the C pad to the V+ pad to ensure that the measured current is 0 rather than infinity when there is nothing attached to the C pad.
    2. Buck Converters
        - A diode is misplaced, killing the buck converters
        - Solution: Place the diode in the correct spot on both bucks
    3. Oscillators
        - There is only a spot for crystals but not for their capacitors, and the wiring is wrong for use with oscillators
        - Solution: Change wiring for oscillator for the RP2040
    4. No pullup on the CS line for the flash
    5. Boot button flipped

### V0.2

-   Goal: A working PCB with some tests to make v0.3 the first final version
    -   It uses the same stencil as v0.1, hence I had to make some compromises with regards to routing and other best practices. I didn't want to spend another 15$ on a stencil, when PCBs are so cheap in comparison.
-   Fixes for all 5 problems with v0.1
-   Same stencil
-   Improvements:
    -   0402 solder bridges instead of 0603
    -   8 layers because that allows for free ENIG finish and POFV at JLCPCB
    -   put baro I2C on aux I2C of gyro? => Solder bridge to test this out

### V0.3

-   Goal: V0.2 (and from a purely flying performance perspective v0.1 too) was generally working very well. Goal is to put in some new features especially blackbox on the SD card due to the slow flash writing. Since the microSD has its own buffer, it should be much faster.
-   Improvements
    -   ELRS with true diversity built in
    -   SD card slot for blackbox
    -   new SPI barometer (Goertek SPL06-001)
    -   synchronous buck converters: smaller (, more efficient)
-   Fixes
    -   removed pullup on current sensor (A relic from the INA139)
-   Known issues
    -   100nF 0402 caps on the bottom layer are very close to each other, causing solder bridges - no issue but not ideal
    -   WiFi antenna poor range (5-10 cm), not sure why
    -   ELRS boot pad is hard to reach
    -   SX1281 crystals 90 degrees rotated --> SX1281 doesn't work at all (jank fix works)
    -   forgot I2C pullups. No issue rn (no sensors using I2C), but with a compass it might be
    -   Bad ELRS range --> a few possible reasons
        -   LNA not working --> most likely (yet reason still unknown), because the RSSI has a very fast jump from about -25 to -75dBm, indicating something else than a pure passives issue. Also, in the transmission path (telemetry), everything works fine, indicating that the PCB and passive components are fine in general
        -   pads grounded insufficiently --> my bad, I didn't compare the library footprint with the datasheet, some pads are not grounded, as they were marked NC in the library but GND in the datasheet --> I put a solder bridge on the pads that are not grounded, and still it doesn't work well, so still unlikely
        -   AT2401C just not working? --> unlikely, but maybe there's a difference between this clone and the RFX2401C
        -   All of them are pretty unlikely, given the weird jump, but I don't know what else it could be
    -   OSD crystal somewhat weird. Nothing I tried worked. I tried putting a crystal from a brand new off the shelf FC on it, as well as using a crystal from V0.2 (via separate wires), as well as changing various components like the AT7456E or capacitors. Sometimes (with the off-the-shelf crystal or the V0.2 crystal), I get video for like 20-60 seconds, but after a while they all stop working until I cut power and wait a few seconds. Nothing gets particularly warm, hence my confusion with the issue. Will go back to the design that worked in V0.2, to give me some space to play with all different sizes

### V0.4

-   Goal: V0.3 introduced a lot of new features, but not all work properly. This PCB will hopefully fix all the new issues that emerged with V0.3. Especially the ELRS range and the OSD crystal, but also implement a proper non-jank fixes for the other stuff. No new features, similar to V0.2 compared to V0.1. Biggest issue is that this time I cannot really explain to myself the two big issues and so I just have to guess.
-   Fixes (at least I hope)
    -   ELRS range -> Test RFX2401C instead of AT2401C, and ground all the pins. I will also swap the RFX2401C onto V0.3 after arrival to see if it's a PCB issue or a component issue
    -   ELRS WiFi -> proper filter according to datasheet
    -   ELRS crystal 90° rotated
    -   ELRS boot pad is now a button
    -   A pair of 4.7kOhm pullups for I2C
    -   OSD crystal -> back to V0.2 design, except with more possibilities of testing, like selectable voltage and selectable whether a crystal or oscillator is used
    -   slightly more spacing for 100nF caps on the bottom layer

### V0.5

-   Changes
    -   Switch to RP2350
    -   some changes to the ELRS receiver, maybe it'll work this time?
    -   First version designed in KiCad
    -   Bus layout changed:
        -   Dedicated 3-wire SPI for gyro (PIO) => DMA polling should be possible now
        -   baro has one I2C with external devices like compass
        -   SDIO for SD card (PIO)
        -   Dedicated SPI for OSD
    -   WS2812 LEDs for the swag
    -   better speaker driver
-   What works: Seemingly everything :tada:
-   Idea dump for future:
    -   Reorder 6 pin for GPS/compass: Currently not immediately compatible with Walksnail M10 (RX/TX and SDA/SCL need to be swapped)
    -   RP235xB: more pins for
        -   normal LEDs again
        -   full duplex spi to gyro
        -   separate external I2C for compass
        -   baro via SPI instead of I2C (together with OSD)
        -   more UARTs via PIO (once SPI is separated, pio2 is completely free)
        -   PWM outputs
    -   Speaker driver with optional 5V input for bench testing or in general
    -   more capacitance on 10V rail
    -   separate gyro LDO, or LPF on its supply
    -   custom pixel OSD using PIO/HSTX :thinking:
    -   possible space savings
        -   smaller crystals
        -   2354 instead of 2350 (no separate flash required)
        -   replace USB on SH plug with solder pads [optionally under the USB port]
        -   (pixel OSD instead of AT7456E)

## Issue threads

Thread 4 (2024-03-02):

Blackbox transmission slow

bastian2001, 2024-03-02:
Transmission and generation of non-recorded data (GEN_FLAGS) are slow
- TinyUSB is faster, but has to be tested (transmission)
- Use Rust to decode and generate flags instead of TS?

bastian2001, 2024-03-23:
Actually, transmission is still the issue due to infrequent serial read requests from JS. PR #18 includes a fix for that. Decoding takes almost no time, so this PR, although it only fixes transmission, increases the loading speed by 4x. Possible future improvements include larger chunks (unlikely to make a big difference), more efficient stream piping or directly mounting the file as a mass storage medium.

Closed 2024-03-25.

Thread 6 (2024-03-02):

Blackbox generated FF term is incorrect

bastian2001, 2024-03-02:
The generated data is the S term, not FF. Current workaround is to directly log the FF term, but this is not a solution

Closed 2024-03-07.

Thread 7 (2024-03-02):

FF term scaling

bastian2001, 2024-03-02:
The values are in the order of thousands, quite unpleasant.

The implemented jank-fix is not yet implemented into the configurator. The ideal solution is probably to not use the immediate last cycle, but instead something like the 5th last (which helps because it filters), as well as a different shift.

Closed 2024-03-16.

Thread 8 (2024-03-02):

Throttle has the potential to overflow

bastian2001, 2024-03-02:
The main throttle (because of bad tuning) currently overflows during altitude hold. Better tuning helps with the symptoms but not with the problem.

Not sure if this also affects individual motors in certain scenarios.

Closed 2024-03-14.

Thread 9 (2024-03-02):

Attitude estimation creates wrong values

bastian2001, 2024-03-02:
The attitude quaternion itself stores the correct angle, but the translation into roll and pitch is wrong. Especially at edge cases (|pitch| ~90°+).

The combined value that is also used for vVel interpolation is also too high, leading to the quad thinking it moves up when it is e.g. 45° right and 45° front, until the lowpass of the baro/GPS corrects this.

Closed 2024-03-14.

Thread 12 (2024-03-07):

inverted blackbox traces are not shown properly

bastian2001, 2024-03-07:
Set minimum value of a trace to a larger value than the maximum, and the values will be clipped incorrectly

Closed 2024-03-07.

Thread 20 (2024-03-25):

Blackbox Viewer quality of life improvements

bastian2001, 2024-03-25:
- [x] indicators about how long a second / 10 seconds or whatever is
- [x] shrink hitboxes for frame borders in timeline when zoomed far in
- [x] remove empty entry in popup when no graph is selected
- [x] improve touch and touchpad performance
    - [x] reject last page gesture from touch and touchpad
    - [x] touch move and zoom
- [x] fix one-off-error when scrolling with scroll wheel

Closed 2024-03-29.

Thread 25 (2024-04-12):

better horizontal velocity estimate

bastian2001, 2024-04-12:
use accelerometer to interpolate and GPS to correct long-term

Closed 2025-04-14.

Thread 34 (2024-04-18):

Switch from current Serial protocol to MSP

bastian2001, 2024-04-18:
Current serial protocol has a few shortcomings:
- missing interoperability with other tools
  - BlHeli Suite32, AM32 Configurator etc.
  - MSP over CRSF (configuration over TCP via ELRS RX)
  - potential sensors / digital OSD
- poor checksumming (simple XOR similar to MSPV1)

Implementing MSP (V2) will fix these problems

Closed 2024-06-02.

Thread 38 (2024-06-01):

PCB V5 ideas

bastian2001, 2024-06-01:
- Switch to RP2350 once available
- a working ELRS receiver (standalone RX has taught me a lot, but the amp is still creating problems and I have no idea why -> gatekeeper for V5, as that is a must)
- a working OSD again (the implementation has been the same since V2 (and it worked there) but neither V3 nor V4 have worked). SPI communication seems to work, but all analog stuff is kinda broken. Sometimes I had video coming through, but that went away after a few seconds, and the OSD was even more short-lived. No idea why, but it does not seem like a software issue but either a hardware or soldering issue.
- Gyro on separate SPI bus, and SD, Baro and OSD shared: Gyro can be read without interruptions from the DMA, and that saves a few µs of execution each cycle, and baro and OSD can be moved to the other core so the PID and IMU core can do specifically that and nothing else
- WS2812 LEDs
- amplifier for the speaker: more voltage = more better. In all seriousness, the externally driven speakers are rather quiet, and more voltage could help here, and also increase audibility of the error/startup sounds

Closed 2025-03-27.

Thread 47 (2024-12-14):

Fix random crashes

bastian2001, 2024-12-14:
No idea since when, but there are random crashes of the core that runs loop1. MSP and all the other stuff on the first core keep running, but the PID, Gyro and DShot output just die for no apparent reason.

bastian2001, 2024-12-22:
A new thing just happened: When arming, the MCU just reboots?!?
Likely a hardware fault, but not sure

bastian2001, 2025-04-14:
Since the issues still appeared on the RP2350, it's likely a software issue. The issue stopped happening now though, since I moved some stuff over from loop1 to loop, so likely it was a peripheral collision between the cores

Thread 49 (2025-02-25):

integrated ELRS LUA in configurator

bastian2001, 2025-02-25:
- send a broadcast ping to discover devices in the ELRS network
- Fetch available options like transmit power
- Expose these options as editable in the Receiver tab - maybe even a graphical representation of the network and/or its devices

All in all similar to the "Other devices" option in the ELRS LUA

bastian2001, 2025-03-21:
Receiver only sends back it wouldn't have any configurable options, and handset + transmitter don't send anything :(

Closed 2025-03-21.

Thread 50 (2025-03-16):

return-to-x

bastian2001, 2025-03-16:
Idea dump:
- Record position on takeoff and allow return to home on a switch or connection loss
- if GPS unavailable at takeoff but then it becomes available: use GPS where RSSI was the best as a reasonable guess. Alternatively create a heatmap? 🤔
- return to pilot based on EdgeTX GPS (future EdgeTX release)
- return to pilot based on RSSI only
  1. Climb to an altitude, then always stay on this altitude
  2. Yaw into the direction the quad originated from (i.e., probably towards the pilot
  3. Fly in the current direction for 10s straight
  4. Check if RSSI improved or not
  5. If it got significantly worse, make a sharp 180° turn, go back to step 2
  6. If it stayed roughly the same, make a sharp 90° turn, go back to step 2
  7. If it improved, save the improvement (delta from start to end of this 10s phase)
  8. If the improvement was lower or roughly the same than the last phase's improvement, turn 45° into the direction of the last 10s phase. If the improvement was greater, turn 45° away from the last phase's direction. If it was the first time reaching step 7, choose a random 45° turn. In all cases, go back to step 2
  - requires barometer but no GPS or compass
  - no GPS means we don't know how fast we go so it has to be a decent speed to overcome wind
  - the 45° may be reduced for each time it hits step 7. Should not ro below 10-20° though
  - yes, this algorithm is based on constantly switching directions. It is similar to an MPPT of solar inverters. We have to do this because we have no setpoint. We have to constantly assume that our direction is not the best
  - radio must not be moved around during this procedure and has to be set to a constant power output
  - all turns must be abrupt — we cannot tolerate rotation during each 10s phase because rotation creates very high deltas in RSSI that have nothing to do with position or distance and only with the gain of antennas => a lot of false assumptions would be made
  - this method doesn't _find_ the pilot, it merely flies in the direction of the pilot and will make weird movements once it is close to the pilot. But this is usually fine as we have video again at this point
  - step 0 could be: hold altitude, fly back in the direction the quad was coming from for the past 3s or so. Gyro is good enough for this. Hold altitude. This may bring the video feed or RX back already. Might even already fix the RF problem altogether

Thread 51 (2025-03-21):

Switch to DShot library

bastian2001, 2025-03-21:
I found this awesome library that simplifies the DShot usage to wayyyy fewer functions 😉

https://github.com/bastian2001/pico-bidir-dshot

Also has EDT support

Closed 2025-03-21.

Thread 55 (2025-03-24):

Weird serial on linux

bastian2001, 2025-03-24:
(Configurator issue)
The configurator sometimes receives MSP commands twice, and some packets are dropped. I don't think it is related to Vue or Svelte, as it happened with all three frontend serial-implementations. It seems to come down to the serialport-rs crate. May switch over to a Tauri child-process instead. Those seem to be controllable from the frontend directly -> lower latency, no fetching overhead, and this is generally a nicer solution for Linux. Not sure about Windows though - I'll probably keep the serialport-rs thing there

bastian2001, 2025-04-25:
fix is implemented in branch more-settings

Closed 2025-05-18.

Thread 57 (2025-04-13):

prevent implicit yaw when pitch-rolling in angle mode

bastian2001, 2025-04-13:
When switching from roll to pitch or vice versa during angle mode, without returning to the original position, an implicit change in heading happens, because the quad keeps the local yaw at zero. The quad should instead keep its heading and have a non-zero local yaw to compensate for that.

Similarly, when yawing while pitched forward/rolled sideways, the quad doesn't apply the yaw in the global sense but in the local coordinate system. E.g. when pitched forward while applying yaw right, the quad should also roll right.

bastian2001, 2025-07-21:
implemented into the return-to-x branch. Will be closed once that is merged (will take a while)

Closed 2025-08-06.

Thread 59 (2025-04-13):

shitty performance of blackbox viewer

bastian2001, 2025-04-13:
with all the new logging features and by getting rid of the file size limit (SD logging), the blackbox viewer has really crappy performance during

1. parsing the blackbox file
2. viewing/scrolling, especially larger chunks
3. Editing filters

Viewing/scrolling and filters may be fixed by using different object structures (e.g. chunks of 1000 frames, and different, smaller, path names). Filters may only update the visible chunks when using SMA or binomial (not possible for PT123). Also, maybe some other algorithm might be faster for the calculation. Additionally, separate canvases could be drawn for each trace, so that only one trace needs to be redrawn for a filter

Parsing could be done in Rust (bin to json), and then interpreting the JSON in JS. Also parsing could be faster if not converting everything to a `number` first, but instead using a UInt8Array or so...

Just some ideas, no concrete plans so far

bastian2001, 2025-05-04:
Putting everything in one array per data line fixed this. Maybe it also has something to do with (U)IntXArrays instead of number[] but whatever, the performance is great now, despite still being single-threaded. Will be merged with more-settings

Closed 2025-05-18.

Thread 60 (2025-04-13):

dynamic idle/fix static idle

bastian2001, 2025-04-13:
static idle affects the PID right now. Minimally, but it does. Rather have a fix cutoff for static idle, or even implement dynamic idle to be able to reduce individual motor throttle to 0

Closed 2025-08-06.

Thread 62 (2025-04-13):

better gyro calibration thresholds

bastian2001, 2025-04-13:
noise keeps preventing the gyro calibration. Better to filter the gyro data (with a strong filter, like 10Hz) and then have a narrower window to trigger calibration. Maybe apply an additional HPF (<1Hz) to basically create a very small window size like 2-5 LSB

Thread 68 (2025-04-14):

WS2812 support

bastian2001, 2025-04-14:
Add features for WS2812 LEDs onboard of v0.5. Currently all LEDs turn blue, activity [0] starts blinking and there's an armed indicator (previously debug LED) [1] going white/off on arm/disarm.

Need more RGB!!!

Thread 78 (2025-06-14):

different blackbox frame types

bastian2001, 2025-06-14:
execution tbd, but it would be beneficial if not all frames would be the same size with the same content types, e.g.:
- flight mode rarely changes, so it would be much easier to just have a flag every now and then to indicate that it has changed
- GPS comes in at 20Hz, currently each GPS info frame is split across multiple blackbox frames (= requires minimum logging rate or drops GPS frames, increased space consumption otherwise)
- ELRS comes in at ~250Hz and consumes much more space than it needs
- creating "highlights" or "bookmarks" in a blackbox recording to look at later, triggered by an RC input

Stuff like this could consume much less storage space and create much lower load on the SD card interface (and potentially flash chip in the future)

difficulties
- parsing the length of a blackbox file is much more complicated, because the blackbox has different sized frames now
  - maybe have a field in the header specifying the length, saved after landing such that it can be displayed quickly in the viewer without loading the whole file

Closed 2025-07-05.

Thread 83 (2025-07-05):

Use DMA to sample barometer and magnetometer

bastian2001, 2025-07-05:
currently, sampling the baro takes about 300us, magnetometer takes about 250. With DMA, this would be <10us, and it would also allow to sample e.g. the temperatures which are currently ignored due to time constraints

Closed 2025-08-06.

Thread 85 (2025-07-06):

Multithreaded Blackbox parser and viewer

bastian2001, 2025-07-06:
Idea dump, not finalized

Parser multithreading:
- Main thread: parse header, find frame bounds, and every 50k frames, send these 50k frame bounds to each flag parsing thread. Also parses highlights and flight mode changes
- Flag parsing thread: gets frame bounds, log file and header, and parses one flag of 50k frames at a time. Once all frames are parsed, the TypedArray for this flag is returned. One of these threads exists for each blackbox flag
Note: might be a good idea to limit the amount of threads to the actual hardware (`navigator.hardwareConcurrency`)

Drawing multithreading: Basically one thread for each layer
- Each visible trace gets its own thread for drawing. It gets handed over one of the TypedArrays as well as all the information needed for drawing that trace (color, thickness, min/max etc). This thread also filters the data
- One thread for drawing all the graph bounds, mouse functionality (mouseMove, zoom rect etc.), highlights and flight mode changes
- One thread (still OffscreenCanvas) for assembling all of them
This way, the interface stays smooth, even if anything changes

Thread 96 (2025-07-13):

Better accelerometer calibration routine

bastian2001, 2025-07-13:
Turn quad slowly in all three dimensions, no harsh movements. Filter out values that are not roughly 1g total. Use the same technique as for the magnetometer. This should give a better center point and generally better calibration than manually leveling the quad

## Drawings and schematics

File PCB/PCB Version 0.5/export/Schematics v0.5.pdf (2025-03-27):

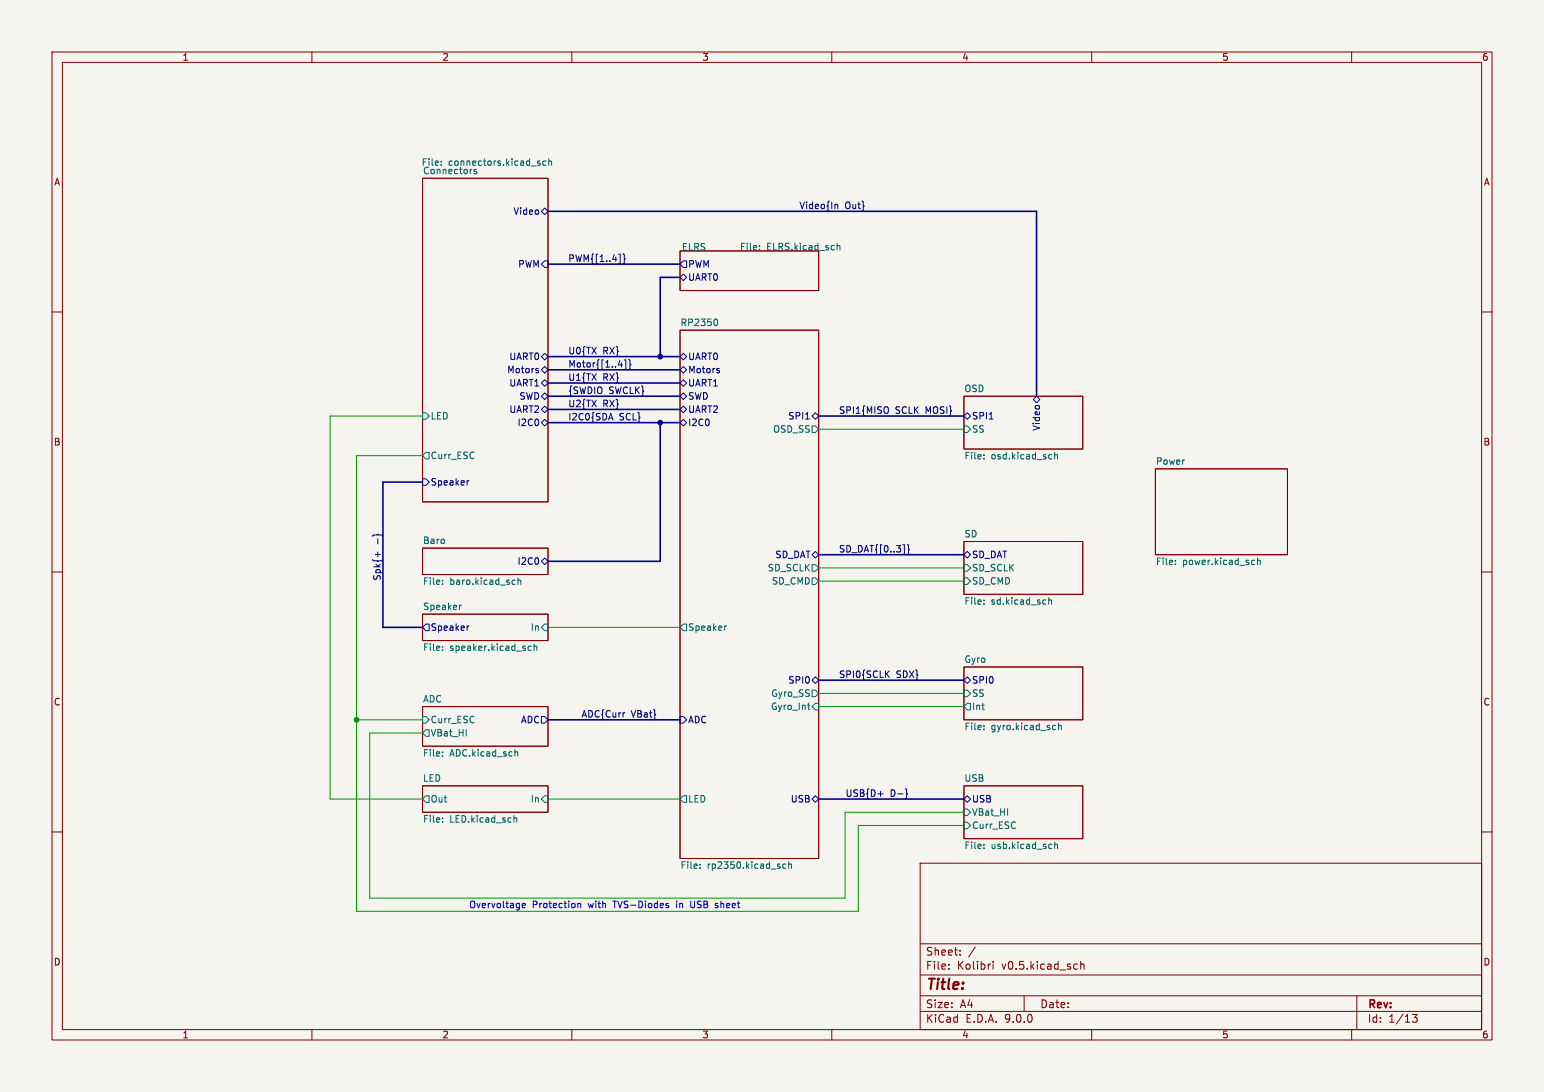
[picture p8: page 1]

I2C0 Baro File: baro.kicad_schVideo UART0 Motors
Gyro_Int SWD

Int Gyro File: gyro.kicad_sch

Id: 1/13 Title: File: Kolibri v0.5.kicad_sch Sheet: /

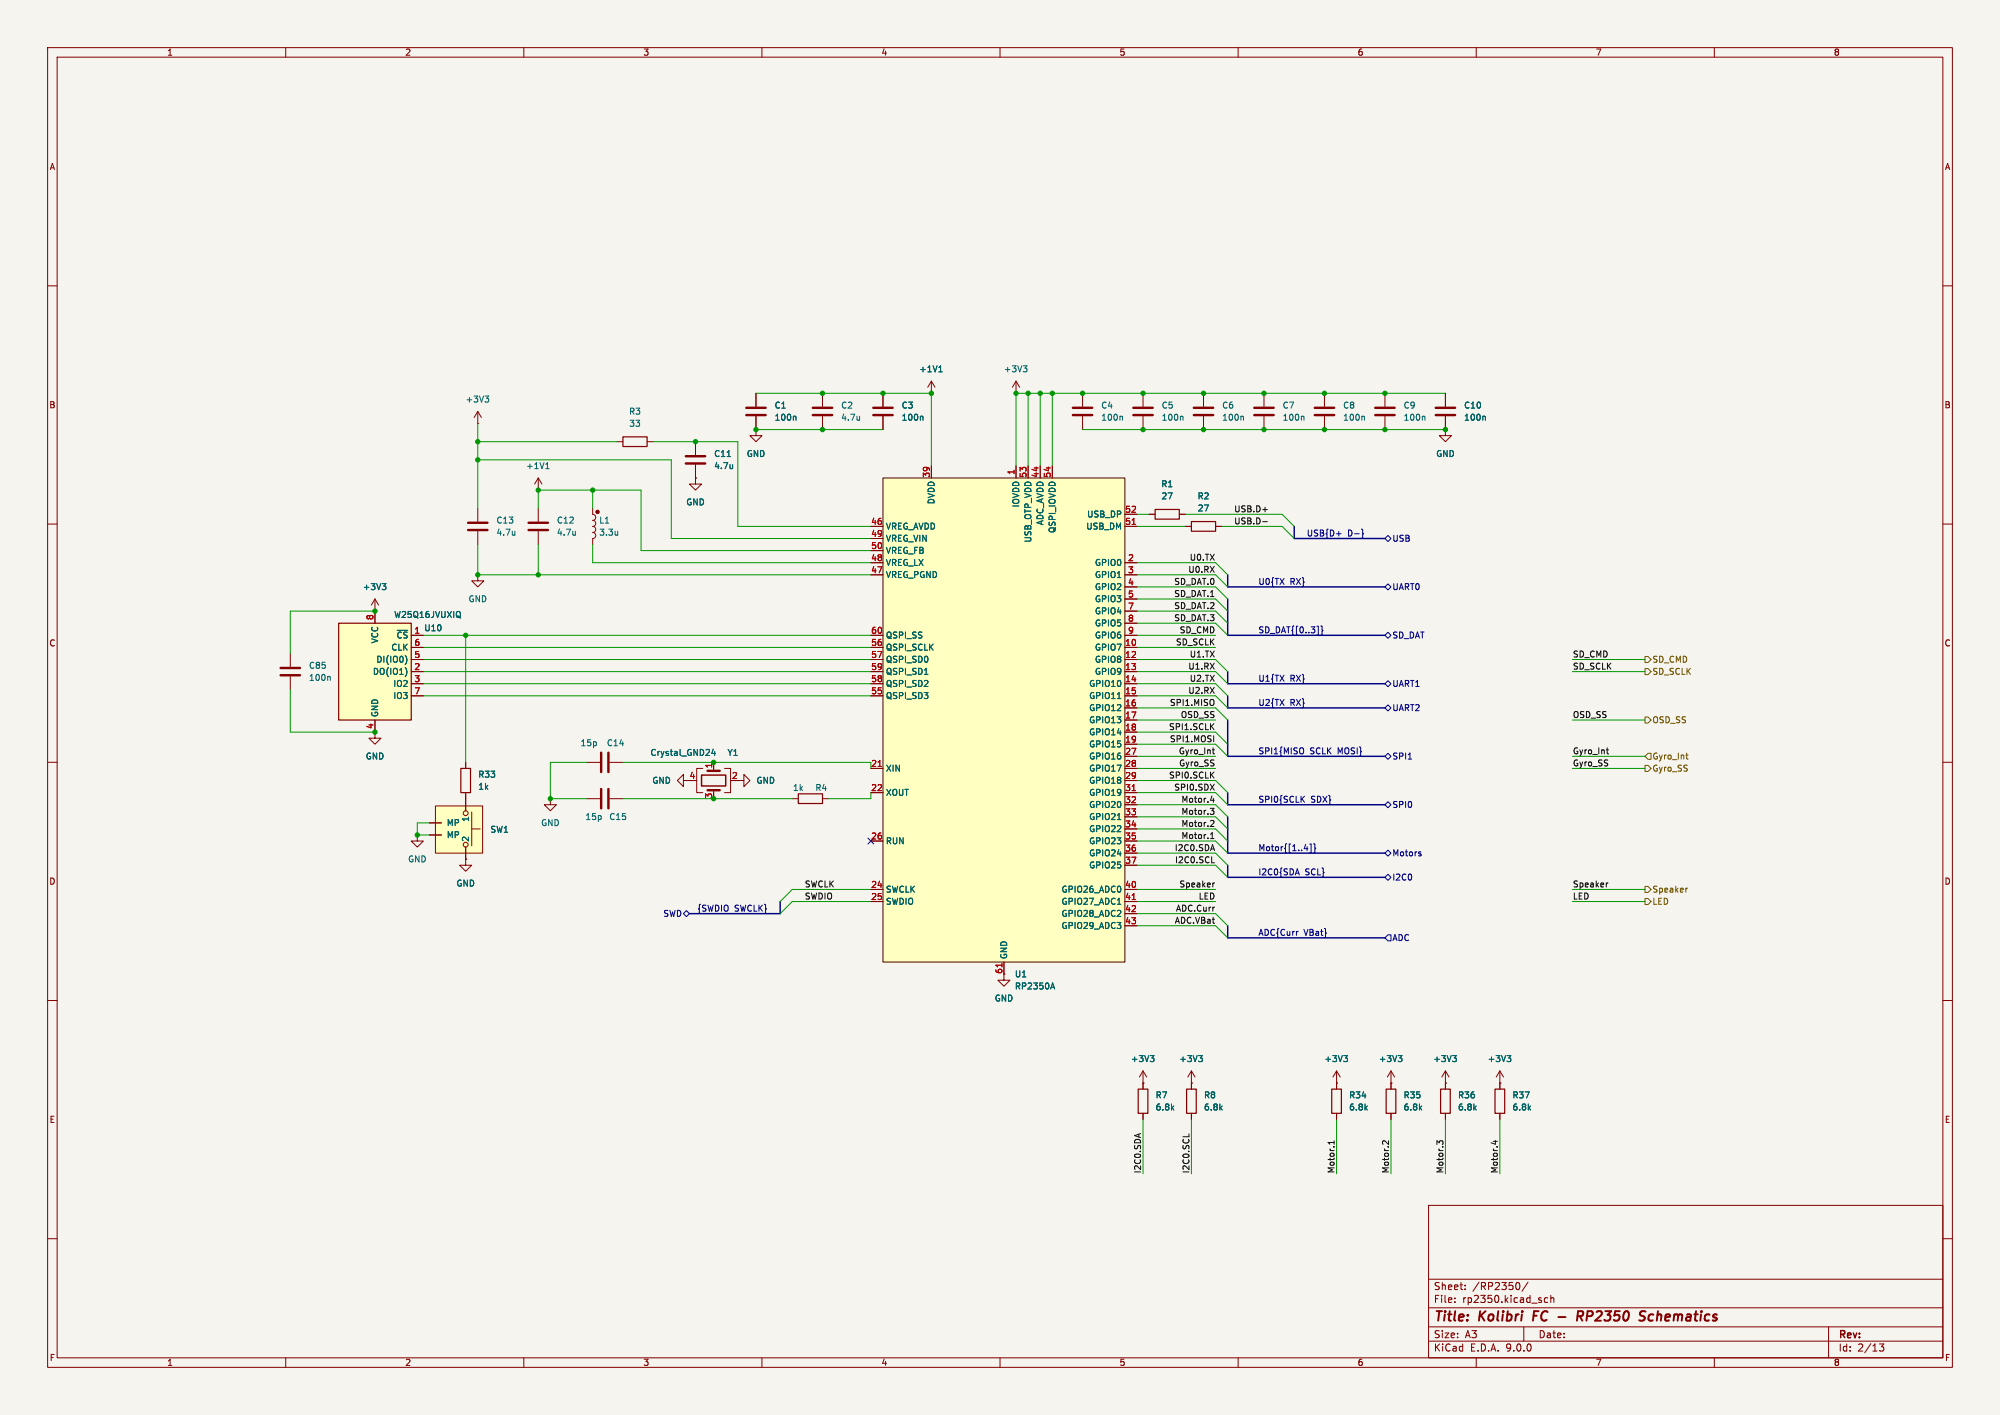
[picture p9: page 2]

{SWDIO SWCLK} U10 W25Q16JVUXIQ
IO3 7 VCC
~{CS}1 CLK 6 DI(IO0) 5 DO(IO1) 2

SPI1{MISO SCLK MOSI} SPI1.SCLK

Id: 2/13 Title: Kolibri FC - RP2350 Schematics

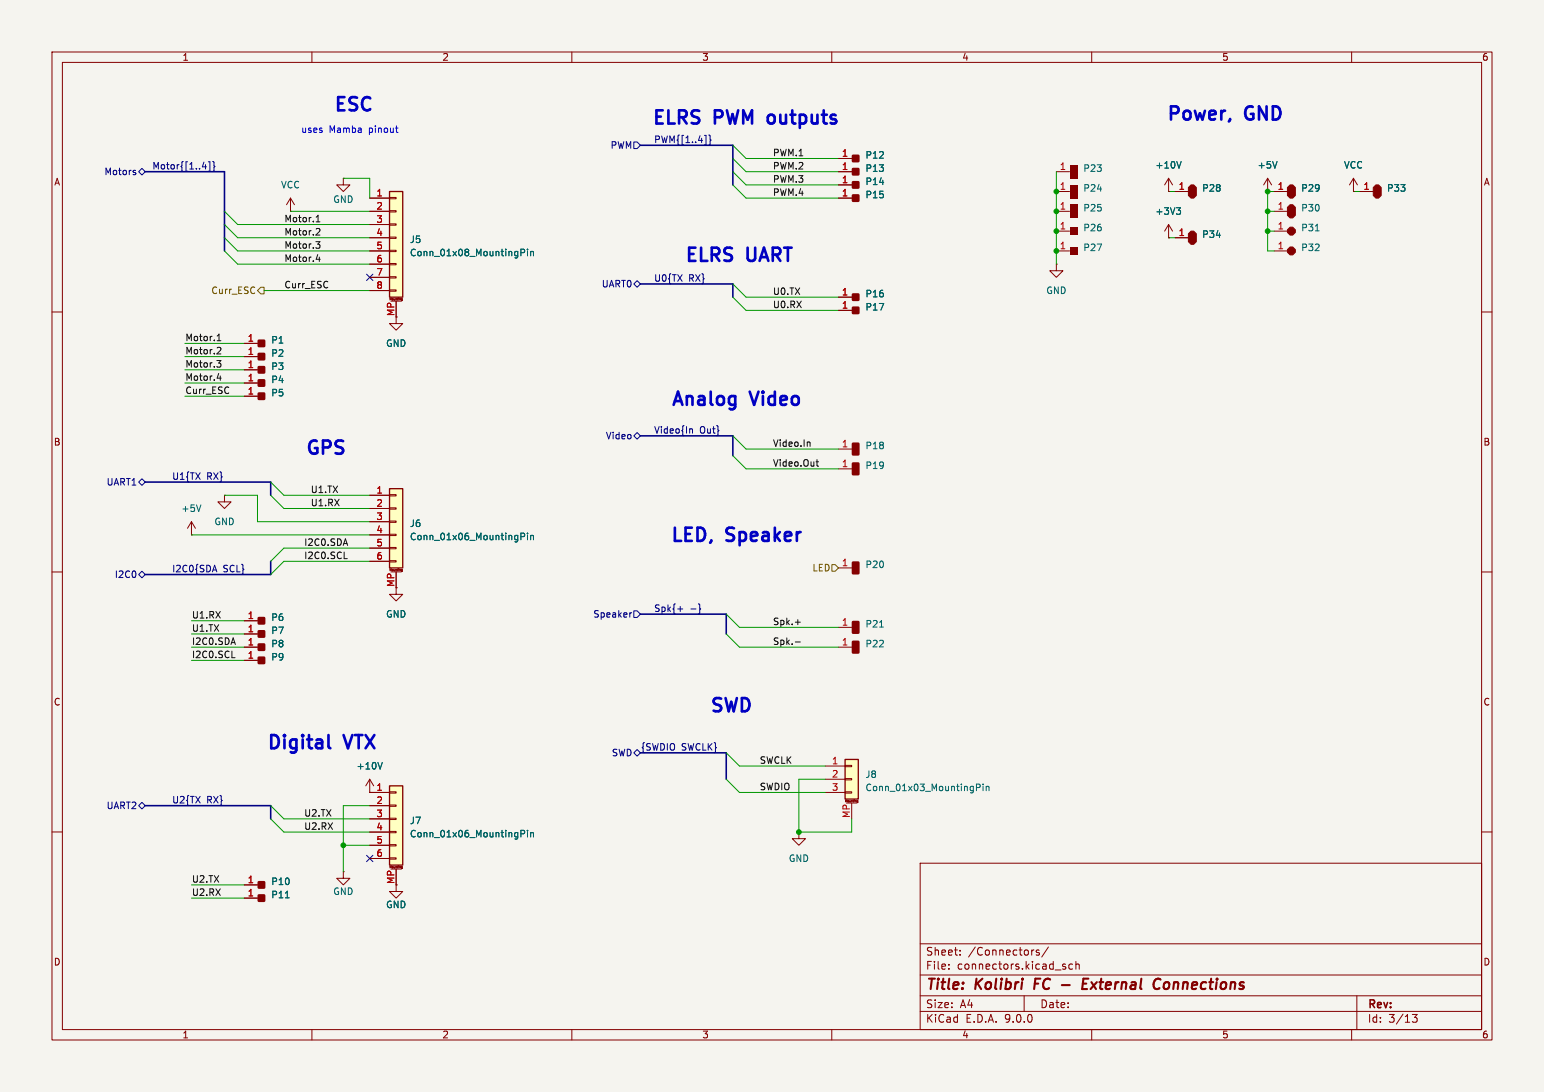
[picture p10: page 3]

ELRS PWM outputs
Video.Out PWM.2 PWM.4
PWM.3 SWDIO

Video.In PWM.1 U0.TX U0.RX

File: connectors.kicad_sch Sheet: /Connectors/ GND

Id: 3/13 Title: Kolibri FC - External Connections

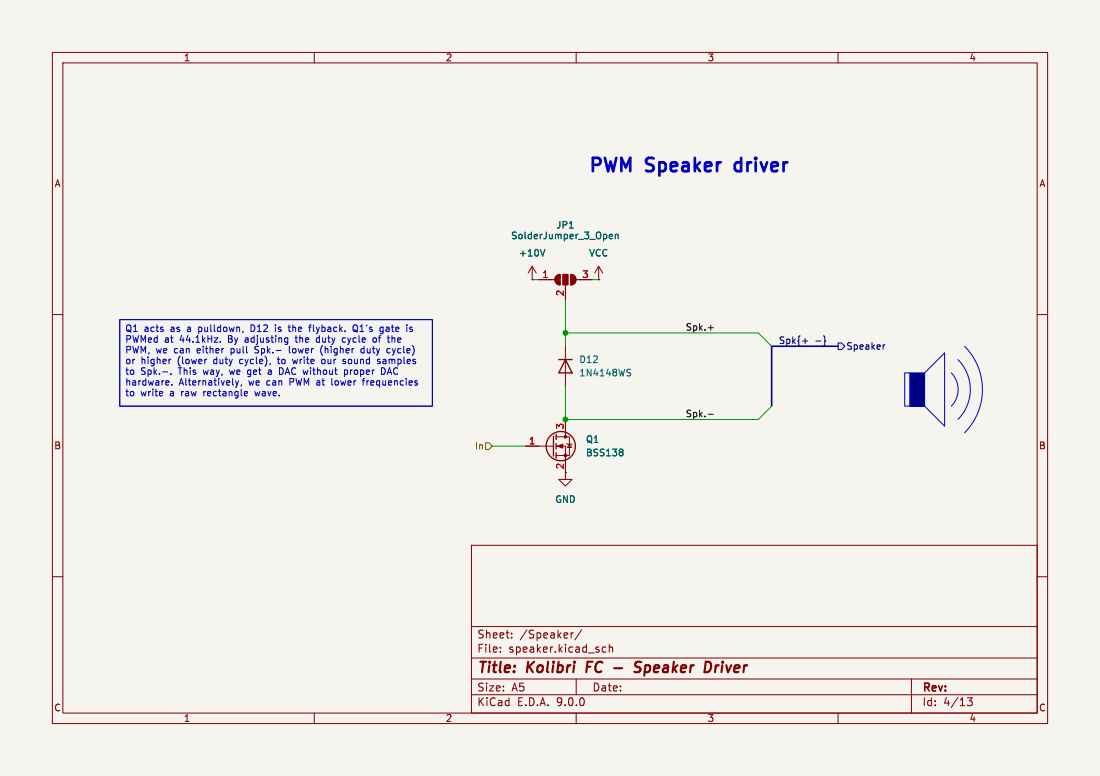
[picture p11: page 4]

JP1 SolderJumper_3_Open

Id: 4/13 Title: Kolibri FC - Speaker Driver File: speaker.kicad_sch Sheet: /Speaker/ 1

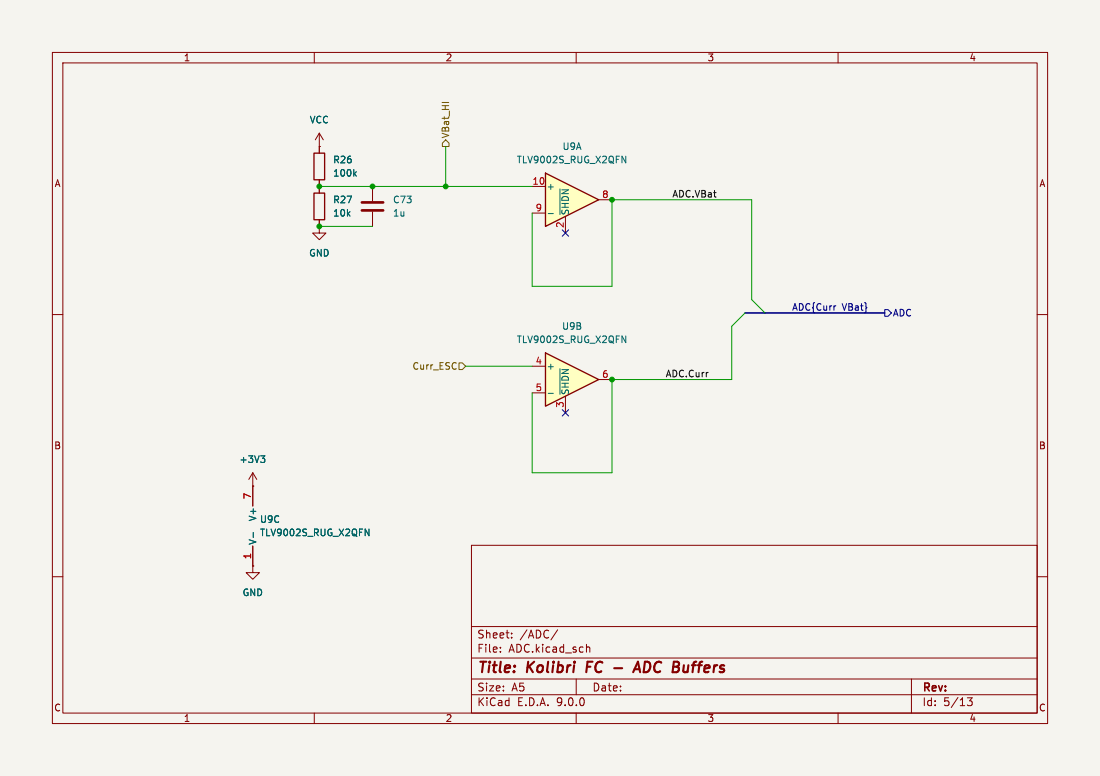
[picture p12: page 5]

File: ADC.kicad_sch Sheet: /ADC/ R27

Id: 5/13 Title: Kolibri FC - ADC Buffers

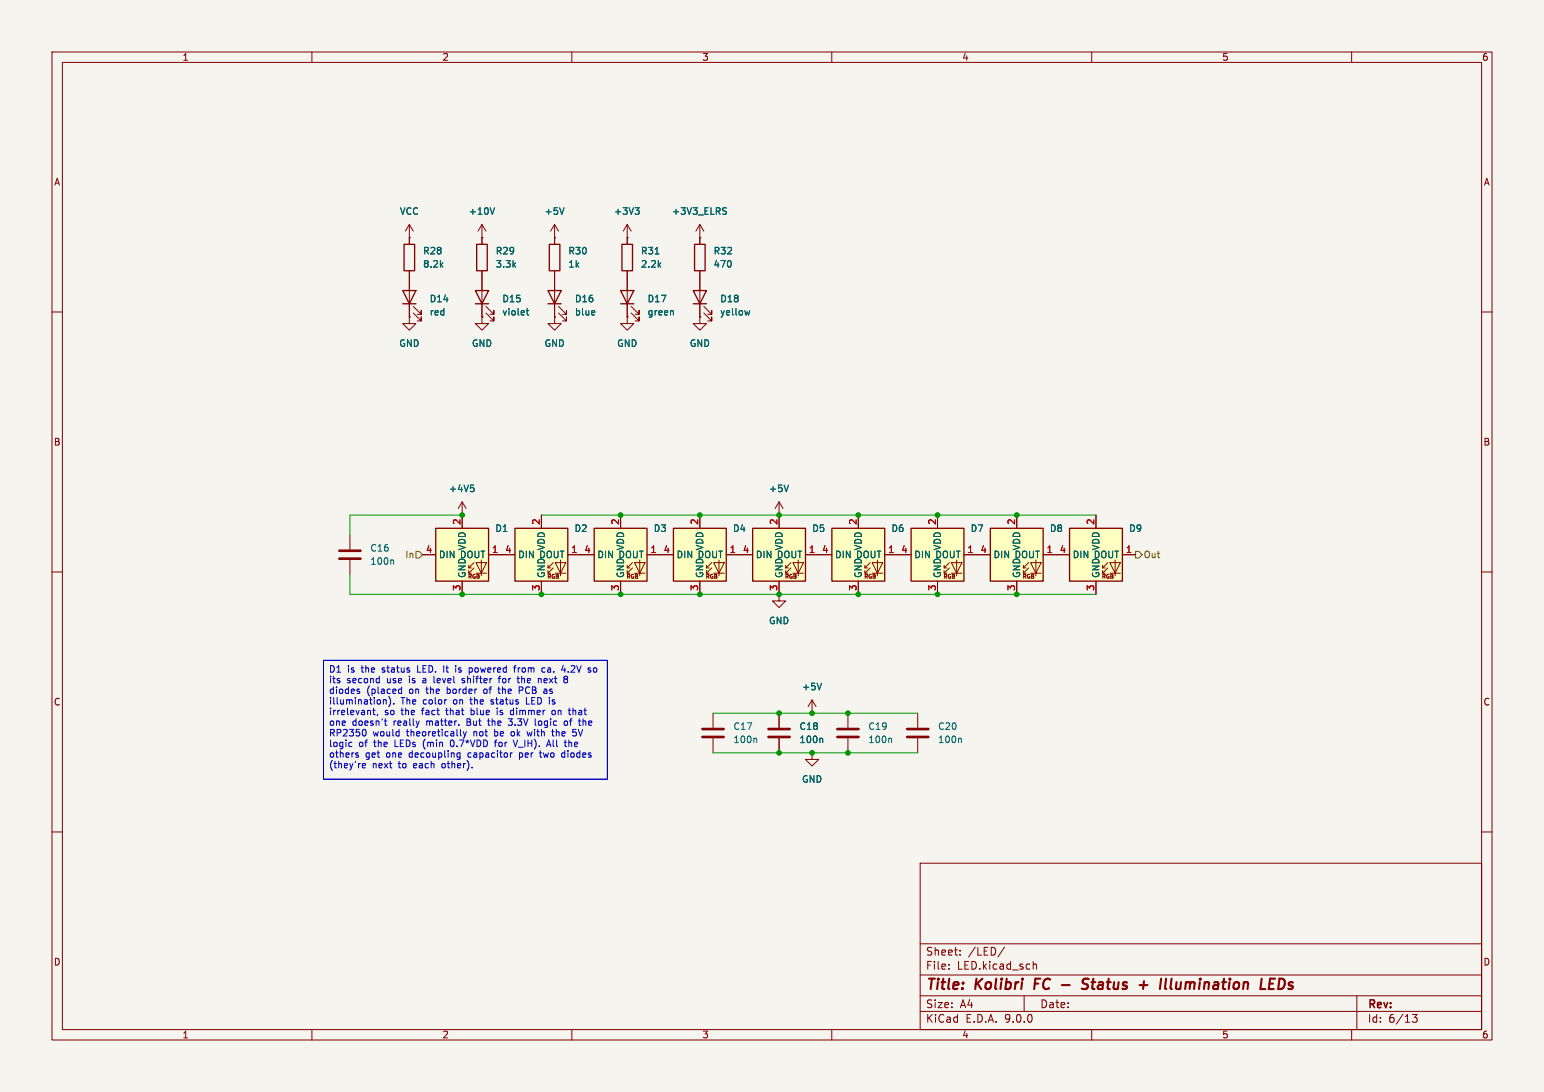
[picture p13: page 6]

File: LED.kicad_sch Sheet: /LED/ +5V D14

its second use is a level shifter for the next 8

logic of the LEDs (min 0.7*VDD for V_IH). All the

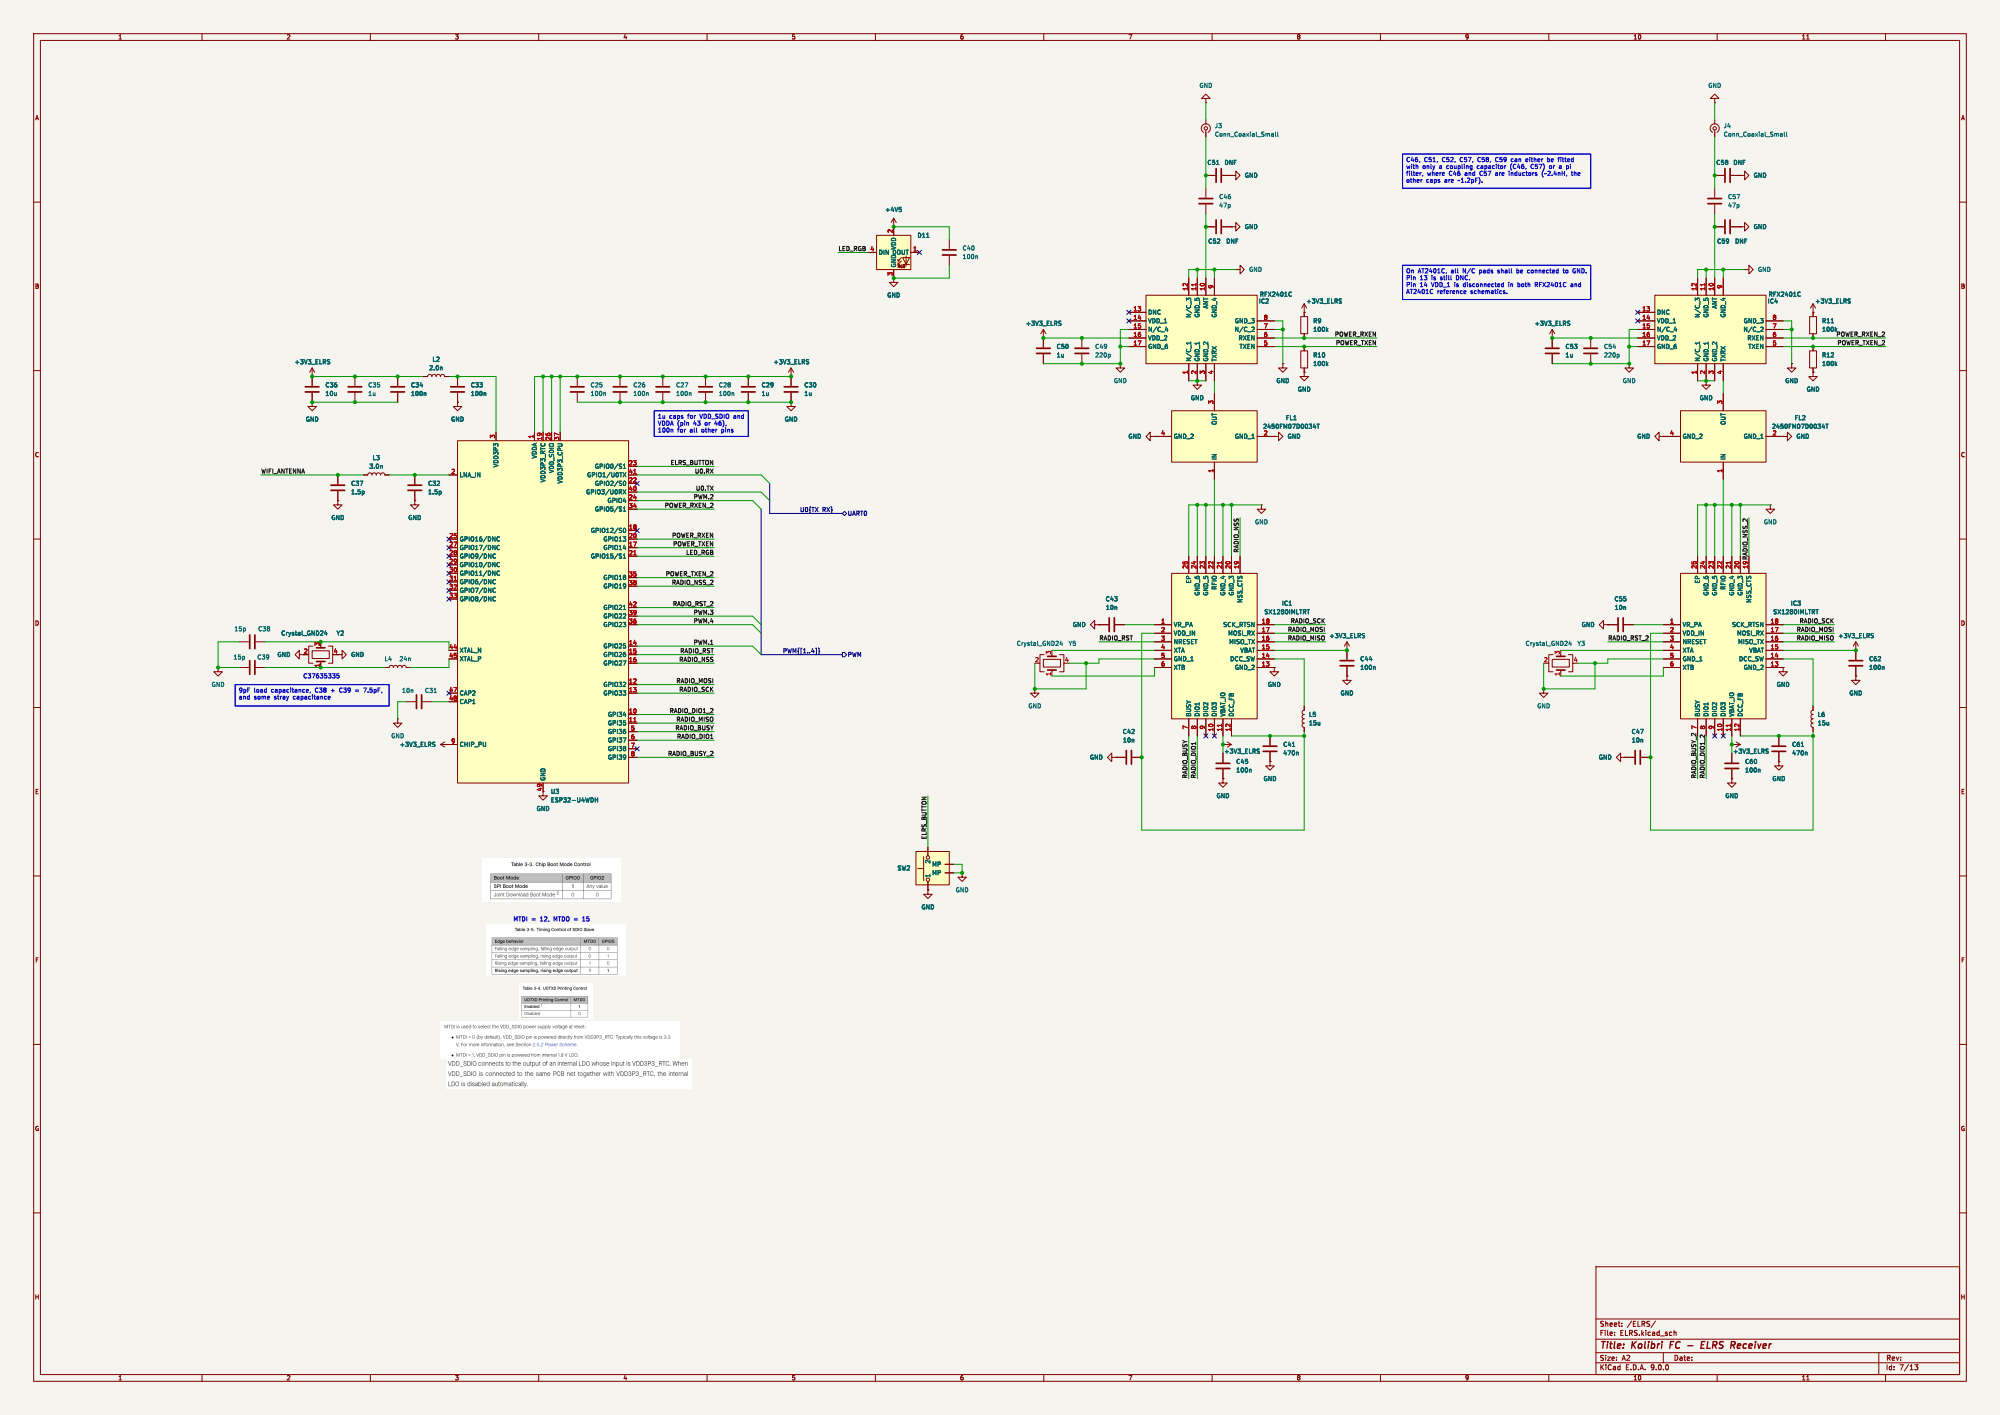
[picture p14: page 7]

1u caps for VDD_SDIO and VDDA (pin 43 or 46), 100n for all other pins
U0.TX RADIO_SCK RADIO_MOSI
LED_RGB RADIO_MISO

1 2 MP MP SW2 GND GND

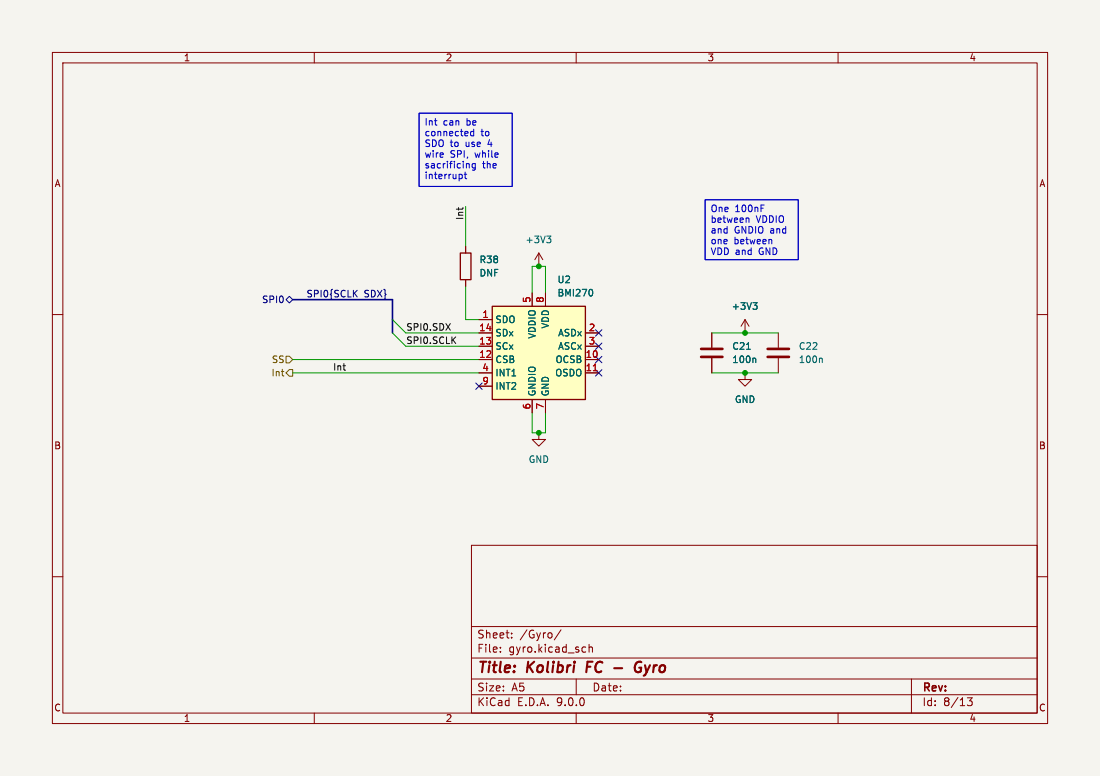
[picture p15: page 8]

between VDDIO
and GNDIO and
one between VDD and GND

7 ASDx 2 ASCx 3 OCSB 10 OSDO 11 U2BMI270 C21

7 ASDx 2 ASCx 3 OCSB 10 OSDO 11 +3V3

Id: 8/13 Title: Kolibri FC - Gyro

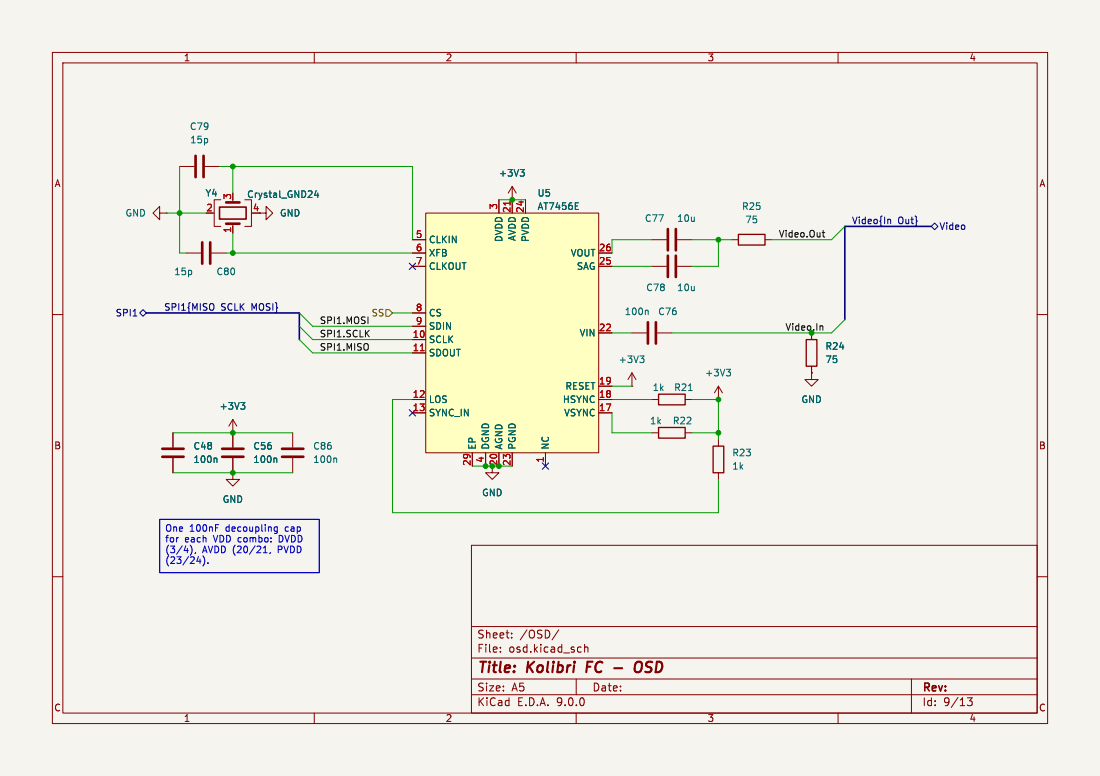
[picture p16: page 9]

1 VOUT 26 SAG 25 VIN 22 RESET 19 HSYNC 18 VSYNC 17 U5AT7456E

3 AGND 20 AVDD 21 PGND 23 PVDD 24 NC

1 VOUT 26 SAG 25 VIN 22 RESET 19 HSYNC 18 VSYNC 17 GND

for each VDD combo: DVDD

Id: 9/13 Title: Kolibri FC - OSD

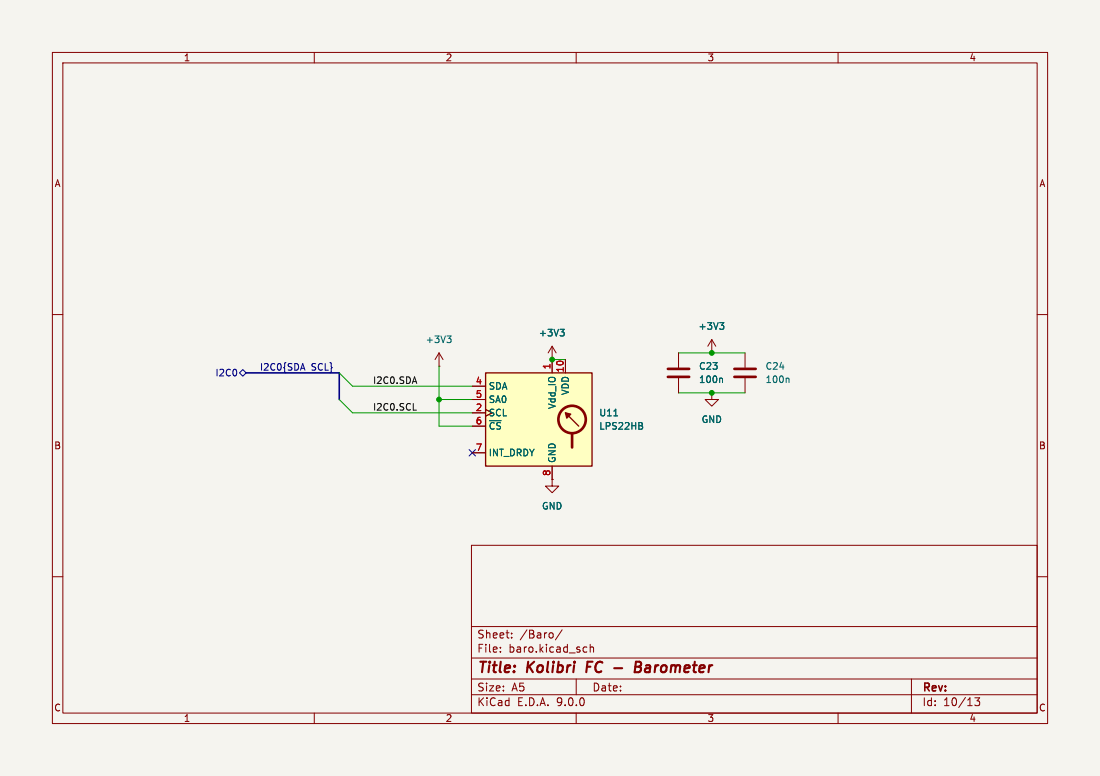
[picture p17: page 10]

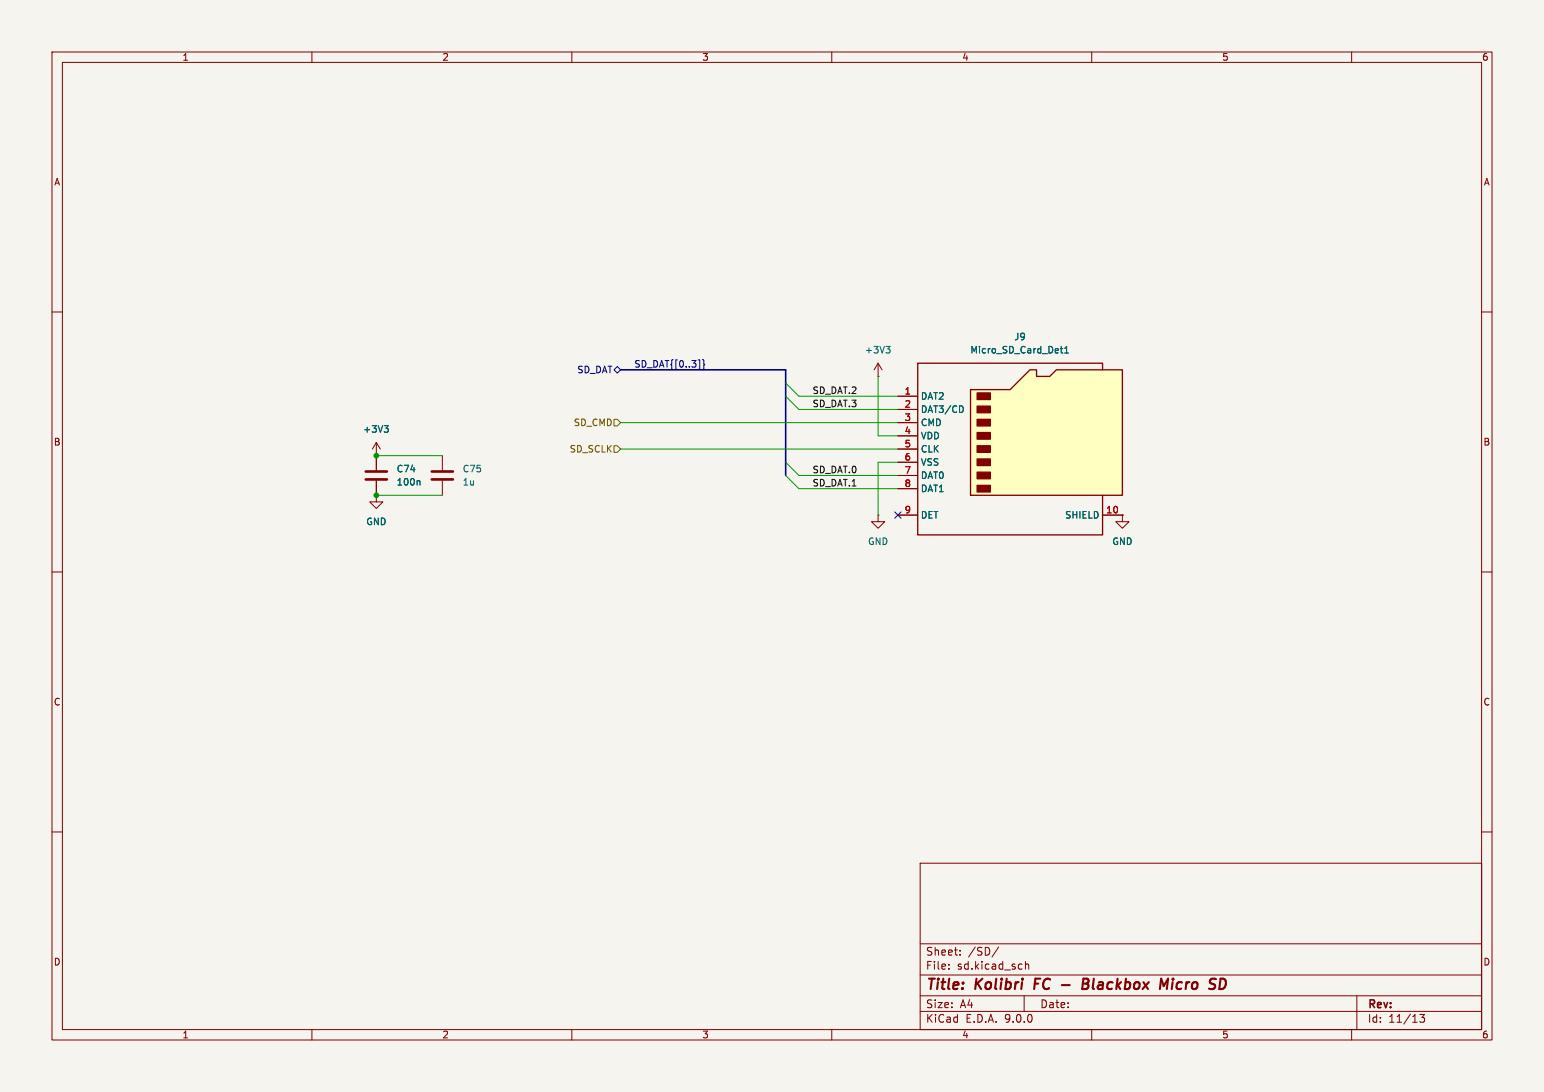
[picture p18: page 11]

File: sd.kicad_sch Sheet: /SD/
Id: 11/13 Title: Kolibri FC - Blackbox Micro SD

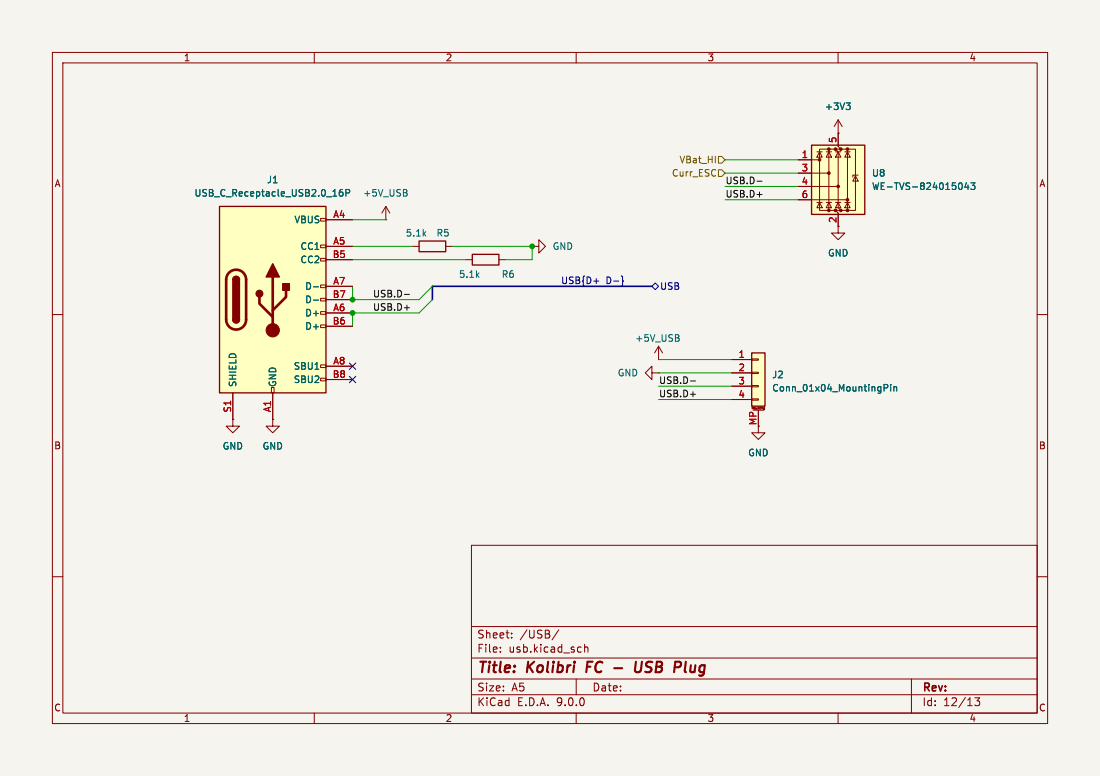
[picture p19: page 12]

5 2 U8 WE-TVS-824015043 GND GND GND SHIELD S1 GND A1 VBUS A4 CC1 A5 CC2 B5 D- A7 D- B7 D+ A6 D+ B6 SBU1 A8 SBU2 B8

File: usb.kicad_sch Sheet: /USB/
Id: 12/13 Title: Kolibri FC - USB Plug


Emergency diode for if that happens during flight.

1 VOUT 2 ST 8 GND GND

separate 3.3V supply. Both LDOs have an almost identical pinout where only PG and GND are swapped, but because both

File: power.kicad_sch Sheet: /Power/
Id: 13/13 Title: Kolibri FC - DCDC + LDO

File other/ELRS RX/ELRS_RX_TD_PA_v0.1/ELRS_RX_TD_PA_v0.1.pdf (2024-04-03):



G N D X 2

ines on one pin)









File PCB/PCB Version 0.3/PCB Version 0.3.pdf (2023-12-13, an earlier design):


Serial1 Motor IO

Spk | | | Spk+ Debug | SDSPI

VI_ADC OSDSPI SDSPI BAROSPI

VI Sensors.SchDoc
Voltage and Current Sensors



8B-SRSS-TB(LF)(SN

6B-SRSS-TB(LF)(SN



3 | D O _(IO 1 ) IO 3 IO 2 CL K G N D DI_(IO 0 ) | 6










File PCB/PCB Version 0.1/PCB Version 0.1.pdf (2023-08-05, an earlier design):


VI Sensors.SchDoc
Voltage and Current Sensors




3 | G N D COMP FB | 8


3 | D O _(IO 1 ) IO 3 IO 2 CL K G N D DI_(IO 0 ) | 6




SDA 3
SCL 4

C17 | | GND 7

VDD 8



8B-SRSS-TB(LF)(SN

6B-SRSS-TB(LF)(SN


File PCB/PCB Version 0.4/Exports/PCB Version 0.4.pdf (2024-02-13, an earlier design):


Serial1 Motor IO

Spk | | | Spk+ Debug | SDSPI

VI_ADC OSDSPI SDSPI BAROSPI

VI Sensors.SchDoc
Voltage and Current Sensors



8B-SRSS-TB(LF)(SN

6B-SRSS-TB(LF)(SN


G N D X 2

C pins are grounded because
RFX2401C clone)
tes


3 | D O _(IO 1 ) IO 3 IO 2 CL K G N D DI_(IO 0 ) | 6










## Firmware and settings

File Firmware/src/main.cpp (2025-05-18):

#include "global.h"
#include "hardware/vreg.h"

volatile u8 setupDone = 0b00;

void setup() {
	Serial.begin(115200);

	runUnitTests();

	vreg_set_voltage(VREG_VOLTAGE_1_30);

	if (powerOnResetMagicNumber == 0xdeadbeefdeadbeef)
		bootReason = rebootReason;
	else
		bootReason = BootReason::POR;
	powerOnResetMagicNumber = 0xdeadbeefdeadbeef;
	rebootReason = BootReason::WATCHDOG;

	Serial.println("Setup started");
	initLittleFs();
	openSettingsFile();
	addSetting(SETTING_UAV_NAME, &uavName, "Kolibri UAV");

	initPid();

	EEPROM.begin(4096);
	// save crash info to EEPROM
	if (crashInfo[0] == 255) {
		Serial.println("Crash detected");
		for (int i = 0; i < 256; i++) {
			EEPROM.write(4096 - 256 + i, (u8)crashInfo[i]);
		}
		EEPROM.commit();
	}
	for (int i = 0; i < 256; i++) {
		crashInfo[i] = 0;
	}
	rtcInit();
	imuInit();
	osdInit();
	initMag();
	initBaro();
	initGPS();
	initADC();
	modesInit();
	initSerial();

	// init ELRS on pins 0 and 1 using Serial1 (UART0)
	ELRS = new ExpressLRS(Serial1, 420000, PIN_TX0, PIN_RX0);

	// init LEDs
	sleep_ms(10);
	p.recalculateClock();
	p.neoPixelFill(0, 0, 255, true);

	initBlackbox();
	initSpeaker();
	rp2040.wdt_begin(200);

	Serial.println("Setup complete");
	extern elapsedMicros taskTimer0;
	taskTimer0 = 0;
	setupDone |= 0b01;
	while (!(setupDone & 0b10)) {
		rp2040.wdt_reset();
	}
	closeSettingsFile();
}

elapsedMillis activityTimer;

elapsedMicros taskTimer0;
void loop() {
	tasks[TASK_LOOP0].runCounter++;
	u32 duration0 = taskTimer0;
	if (duration0 > tasks[TASK_LOOP0].maxGap) {
		tasks[TASK_LOOP0].maxGap = duration0;
	}
	taskTimer0 = 0;
	speakerLoop();
	evalBaroLoop();
	readBaroLoop(); // read after eval to prevent long execution times
	blackboxLoop();
	ELRS->loop();
	modesLoop();
	adcLoop();
	serialLoop();
	configuratorLoop();
	gpsLoop();
	magLoop();
	osdLoop();
	taskManagerLoop();
	rp2040.wdt_reset();
	if (activityTimer >= 500) {
		static bool on = false;
		if (on) {
			p.neoPixelSetValue(0, 0, 0, 0, true);
			on = false;
		} else {
			p.neoPixelSetValue(0, 255, 255, 255, true);
			on = true;
		}
		activityTimer = 0;
	}
	duration0 = taskTimer0;
	tasks[TASK_LOOP0].totalDuration += duration0;
	if (duration0 > tasks[TASK_LOOP0].maxDuration) {
		tasks[TASK_LOOP0].maxDuration = duration0;
	}
	if (duration0 < tasks[TASK_LOOP0].minDuration) {
		tasks[TASK_LOOP0].minDuration = duration0;
	}
	taskTimer0 = 0;
}

u32 *speakerRxPacket;
void setup1() {
	while (!(setupDone & 0b01)) {
	}
	initESCs();
	gyroInit();
	setupDone |= 0b10;
	while (!(setupDone & 0b01)) {
	}
}
elapsedMicros taskTimer = 0;

extern PIO speakerPio;
extern u8 speakerSm;
void loop1() {
	tasks[TASK_LOOP1].runCounter++;
	u32 duration = taskTimer;
	if (duration > tasks[TASK_LOOP1].maxGap) {
		tasks[TASK_LOOP1].maxGap = duration;
	}
	taskTimer = 0;
	gyroLoop();

	if (gyroUpdateFlag & 0x01) {
		gyroUpdateFlag &= ~0x01;
		imuUpdate();
		decodeErpm();
		pidLoop();
	}

	duration = taskTimer;
	tasks[TASK_LOOP1].totalDuration += duration;
	if (duration > tasks[TASK_LOOP1].maxDuration) {
		tasks[TASK_LOOP1].maxDuration = duration;
	}
	if (duration < tasks[TASK_LOOP1].minDuration) {
		tasks[TASK_LOOP1].minDuration = duration;
	}
	taskTimer = 0;
}

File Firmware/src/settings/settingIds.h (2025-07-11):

// accelerometer settings
#define SETTING_ACC_CAL "accel_calibration"
#define SETTING_ACC_FILTER_CUTOFF "accel_filter_cutoff"

// blackbox settings
#define SETTING_BB_FLAGS "blackbox_flags"
#define SETTING_BB_DIV "blackbox_freq_divider"

// GPS settings
#define SETTING_GPS_UPDATE_RATE "gps_update_rate"
#define SETTING_GPS_VEL_FILTER_CUTOFF "gps_velocity_filter_cutoff"

// magnetometer settings
#define SETTING_MAG_CAL_HARD "compass_calibration_hard"
#define SETTING_MAG_FILTER_CUTOFF "compass_filter_cutoff"

// motor and ESC settings
#define SETTING_BEEP_TONE "dshot_beep_tone"

// battery settings
#define SETTING_EMPTY_VOLTAGE "bat_empty_voltage"

// flight performance settings
#define SETTING_PID_GAINS "pid_gains"
#define SETTING_IDLE_PERMILLE "motor_idle_per_mille"
#define SETTING_IFALLOFF "pid_ifalloff"
#define SETTING_MAX_ANGLE "angle_max_angle"
#define SETTING_RATE_COEFFS "rate_coeffs"
#define SETTING_DFILTER_CUTOFF "filter_d_cutoff"
#define SETTING_GYRO_FILTER_CUTOFF "filter_gyro_cutoff"
#define SETTING_SETPOINT_DIFF_CUTOFF "setpoint_diff_cutoff"
#define SETTING_PID_BOOST_CUTOFF "pid_boost_cutoff"
#define SETTING_PID_BOOST_START "pid_boost_start"
#define SETTING_PID_BOOST_FULL "pid_boost_full"
#define SETTING_PID_VVEL "althold_pid"
#define SETTING_VVEL_FF_FILTER_CUTOFF "althold_vvel_ff_cutoff"
#define SETTING_VVEL_D_FILTER_CUTOFF "althold_vvel_d_cutoff"
#define SETTING_MAX_TARGET_HVEL "poshold_max_target_hvel"
#define SETTING_PID_HVEL "poshold_pid"
#define SETTING_HVEL_FF_FILTER_CUTOFF "poshold_hvel_ff_cutoff"
#define SETTING_HVEL_I_RELAX_FILTER_CUTOFF "poshold_hvel_irelax_cutoff"
#define SETTING_HVEL_PUSH_FILTER_CUTOFF "poshold_hvel_push_cutoff"
#define SETTING_MAX_ANGLE_BURST "poshold_max_angle_burst"
#define SETTING_ANGLE_BURST_TIME "poshold_angle_burst_time"
#define SETTING_ANGLE_BURST_COOLDOWN "poshold_angle_cooldown_time"
#define SETTING_HVEL_STICK_DEADBAND "poshold_hvel_stick_deadband"

// general settings
#define SETTING_UAV_NAME "uav_name"
#define SETTING_TIMEZONE_OFFSET "timezone_offset_mins"
#define SETTING_START_SOUND "start_wav"
#define SETTING_START_FALLBACK_RTTTL "start_sound_fallback"

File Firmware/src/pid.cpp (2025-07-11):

#include "global.h"

FlightMode flightMode = FlightMode::ACRO;

/*
 * To avoid a lot of floating point math, fixed point math is used.
 * The gyro data is 16 bit, with a range of +/- 2000 degrees per second.
 * All data is converted to degrees per second (both RC commands as well as gyro data),
 * and calculations will be performed on a 16.16 fixed point number.
 * Additions can be performed like normal, while multiplications require
 * the numbers to be converted to 64 bit before calculation.
 */

i16 throttles[4];

fix32 gyroScaled[3];

fix32 pidGains[3][5];
fix32 iFalloff;
fix32 pidGainsVVel[4], pidGainsHVel[4];
fix32 angleModeP = 10, velocityModeP = 10;

fix32 rollSetpoint, pitchSetpoint, yawSetpoint, rollError, pitchError, yawError, rollLast, pitchLast, yawLast, vVelSetpoint, vVelError, vVelLast, eVelSetpoint, eVelError, eVelLast, nVelSetpoint, nVelError, nVelLast, vVelLastSetpoint;
fix64 rollErrorSum, pitchErrorSum, yawErrorSum, vVelErrorSum, eVelErrorSum, nVelErrorSum;
fix32 rollP, pitchP, yawP, rollI, pitchI, yawI, rollD, pitchD, yawD, rollFF, pitchFF, yawFF, rollS, pitchS, yawS, vVelP, vVelI, vVelD, vVelFF, eVelP, eVelI, eVelD, eVelFF, nVelP, nVelI, nVelD, nVelFF;
fix32 altSetpoint;
fix32 throttle;
fix64 targetLat, targetLon;
u16 dFilterCutoff;
PT2 dFilterRoll, dFilterPitch, dFilterYaw;
u16 gyroFilterCutoff;
PT1 gyroFiltered[3];

fix32 setpointDiffCutoff = 12;
PT1 setpointDiff[3];
fix32 lastSetpoints[3];

fix32 pidBoostCutoff = 5; // cutoff frequency for pid boost throttle filter
PT1 pidBoostFilter;
fix32 lastThrottle;
u8 pidBoostAxis = 1; // 0: off, 1: RP only, 2: RPY
fix32 pidBoostP = 2.5; // addition boost factor, e.g. when set to 2 in full effect, P is 3x
fix32 pidBoostI = 2.5; // addition boost factor, e.g. when set to 2 in full effect, I is 3x
fix32 pidBoostD = 0; // addition boost factor, e.g. when set to 2 in full effect, D is 3x
fix32 pidBoostStart; // dThrottle/dt in 1/1024 / s when pidBoost starts
fix32 pidBoostFull; // dThrottle/dt in 1/1024 / s when pidBoost is in full effect

u32 pidLoopCounter = 0;

fix32 rateCoeffs[3][3];
fix32 rateInterp[3][258]; // +-128 (=257) for sticks, index 257 only exists so that high + 1 is valid even if stick = 1
fix64 vVelMaxErrorSum, vVelMinErrorSum;
u8 maxAngle; // degrees, applied in angle mode and GPS mode
u8 maxAngleBurst; // degrees, this angle is allowed for a short time, e.g. when accelerating in GPS mode (NOT used in angle mode)
fix32 stickToAngle;
u16 idlePermille;
fix32 throttleScale;
fix32 maxTargetHvel; // maximum target horizontal velocity (m/s)
fix32 smoothChannels[4];
elapsedMillis burstTimer;
elapsedMillis burstCooldown;
u16 angleBurstTime; // milliseconds, time for which the maxAngleBurst is allowed
u16 angleBurstCooldownTime; // milliseconds, time for which the maxAngleBurst is not allowed after the burst time

fix32 vvelDFilterCutoff;
fix32 vvelFFFilterCutoff;
PT1 vVelDFilter;
PT1 vVelFFFilter;

fix32 hvelFfFilterCutoff;
fix32 hvelIRelaxFilterCutoff;
fix32 hvelPushFilterCutoff;
u16 hvelStickDeadband; // deadband for the horizontal velocity stick input (total stick is -512 to 512)
PT1 ffFilterNVel;
PT1 ffFilterEVel;
DualPT1 iRelaxFilterNVel;
DualPT1 iRelaxFilterEVel;
PT1 pushNorth;
PT1 pushEast;

interp_config rateInterpConfig0, rateInterpConfig1, rateInterpConfig2;

void initPidGains() {
	for (int i = 0; i < 3; i++) {
		pidGains[i][P].setRaw(80 << P_SHIFT);
		pidGains[i][I].setRaw(40 << I_SHIFT);
		pidGains[i][D].setRaw(500 << D_SHIFT);
		pidGains[i][FF].setRaw(40 << FF_SHIFT);
		pidGains[i][S].setRaw(0 << S_SHIFT);
	}
}

void initRateCoeffs() {
	for (int i = 0; i < 3; i++) {
		rateCoeffs[i][ACTUAL_CENTER_SENSITIVITY] = 170;
		rateCoeffs[i][ACTUAL_MAX_RATE] = 900;
		rateCoeffs[i][ACTUAL_EXPO] = 0.57;
	}
}

/**
 * @brief calculates the rate based on ACTUAL rates, does NOT use the LUT
 *
 * @param stick from -1 to 1, where 0 is center and +-1 is full stick
 * @param axis AXIS_ROLL, AXIS_PITCH or AXIS_YAW (0, 1 or 2)
 * @return fix32 the rate in degrees per second
 */
static fix32 calculateActual(fix32 stick, u8 axis) {
	fix32 center = rateCoeffs[axis][ACTUAL_CENTER_SENSITIVITY];
	fix32 maxRate = rateCoeffs[axis][ACTUAL_MAX_RATE];
	fix32 expo = rateCoeffs[axis][ACTUAL_EXPO];
	fix32 stick2 = stick * stick;
	fix32 stick6 = stick2 * stick2 * stick2;
	if (expo < 0) expo = 0;
	if (expo > 1) expo = 1;
	fix32 linPart = stick * center;
	fix32 expoPart = (expo * stick6 + (fix32(1) - expo) * stick2) * (maxRate - center) * stick.sign();
	return linPart + expoPart;
}

static void startRateInterp() {
	interp_set_config(interp0, 0, &rateInterpConfig0);
	interp_set_config(interp0, 1, &rateInterpConfig1);
	interp_set_config(interp1, 0, &rateInterpConfig2);
	interp1->base[0] = -1 << 15;
	interp1->base[1] = 1 << 15;
}

/**
 * @brief Get the target rotational rate for a given stick value and axis.
 *
 * Uses the interpolator for faster access to the pre-calculated rates. Run startRateInterp() before every batch of using this function.
 *
 * @param stick stick position from -1 to 1, where 0 is center and +-1 is full stick
 * @param axis AXIS_ROLL, AXIS_PITCH or AXIS_YAW (0, 1 or 2)
 * @return fix32 the rate in degrees per second
 */
static fix32 getRateInterp(fix32 stick, u8 axis) {
	// we use interp1 lane 0 for shifting and clamping the -1...1 (17 bit) stick value. Shifting so it is a 16 bit number, and clamping so that we do not get out of bounds
	interp1->accum[0] = stick.raw;
	// the peek value is shifted and clamped to -0.5...0.5 (-32768...32768), after shifting it is -128...128, then move that range to 0...256 for the LUT
	i32 high = ((i32)interp1->peek[0] >> 8) + 128; // high byte (from 0-255 for -1 to <1 stick, 256 only for stick = 1)

	interp0->accum[1] = interp1->peek[0]; // interpolation alpha value (only 8 LSBs (the ones we removed in the high byte) are used), this is the low byte
	interp0->base[0] = rateInterp[axis][high].raw; // lower bound from LUT
	interp0->base[1] = rateInterp[axis][high + 1].raw; // upper bound from LUT
	return fix32().setRaw(interp0->peek[1]); // alpha applied between lower and upper
}

static void fillRateInterp() {
	for (int i = 0; i < 3; i++) {
		for (int j = 0; j < 257; j++) {
			fix32 stick = fix32(j - 128) / 128; // from -1 to 1
			rateInterp[i][j] = calculateActual(stick, i);
		}
	}
	startRateInterp();

	elapsedMicros e;
	i32 time = 0, time2 = 0;
	e = 0;
	fix32 sum = 0;
	fix32 sum2 = 0;
	for (fix32 i = -1; i <= 1; i += fix32(1) / 1024) {
		sum += getRateInterp(i, AXIS_ROLL);
	}
	time = e;
	e = 0;
	for (fix32 i = -1; i <= 1; i += fix32(1) / 1024) {
		sum2 += calculateActual(i, AXIS_ROLL);
	}
	time2 = e;
	Serial.printf("Time for interp: %d us, Time for calculateActual: %d us, diff: %d us\n", time, time2, time - time2);
	Serial.printf("Sum for interp: %.3f, Sum for calculateActual: %.3f, diff: %.3f\n", sum.getf32(), sum2.getf32(), (sum - sum2).getf32());
}
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

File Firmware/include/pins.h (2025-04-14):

#include "typedefs.h"

#define PIN_TX0 0 // UART0 / Serial1
#define PIN_RX0 1 // UART0 / Serial1
#define PIN_TX1 8 // UART1 / Serial2
#define PIN_RX1 9 // UART1 / Serial2
#define PIN_TX2 10 // SoftwareSerial
#define PIN_RX2 11 // SoftwareSerial

#define PIN_OSD_MISO 12
#define PIN_OSD_CS 13
#define PIN_OSD_SCLK 14
#define PIN_OSD_MOSI 15

#define PIN_GYRO_INT1 16
#define PIN_GYRO_CS 17
#define PIN_GYRO_SCLK 18
#define PIN_GYRO_SDX 19

#define PIN_SD_DAT 2
#define PIN_SD_CMD 6
#define PIN_SD_SCLK 7

#define PIN_SDA0 24
#define PIN_SCL0 25

#define PIN_ADC_CURRENT 28
#define PIN_ADC_VOLTAGE 29

#define PIN_MOTORS 20 // pin at which the motor outputs start

#define PIN_SPEAKER 26
#define PIN_LEDS 27

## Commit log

2023-07-06 add PCB v0.1
    [Baro.SchDoc, Connectors.SchDoc, Custom Components.PcbLib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]
2023-07-06 added INA139 Simulation
    [INA139.DSN]
2023-07-08 PCB v0.2, not done yet
    still missing: Vias are untented, remove 0R resistors for voltage rails after v0.1 testing
    [Baro.SchDoc, Connectors.SchDoc, Custom Components.PcbLib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]
2023-08-05 Schematics PDF and solder rig for the stencil
    [Alignment card.prt, Alignment card.stl]
2023-08-05 some PCB v0.2 improvements
    [OSD.SchDoc, RP2040.SchDoc, Voltage Regulators.SchDoc]
2023-08-08 added pictures of board
    [PCB Version 0.1.PrjPcb, Voltage Regulators.SchDoc]
2023-08-09 Started work in firmware
    DShot and BMI270 drivers
    - Up to DShot 2400 using just 4 instructions on one PIO, to drive all 4 motors
    - BMI270 driver using SPI and apparently the RP2040 can only to 8MHz SPI, and only while blocking the main processor :angry:. Maybe some future work for an asynchronous PIO SPI?
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2023-08-09 added ESC and Speaker driver, motor output
    Motor output purely based on throttle for now
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2023-08-11 code cleanup, adjusted PIDs
    adjusted PIDs according to "my feeling while spinning unloaded motors in my room"
2023-08-12 i falloff fix, speaker on a switch
    [pid.cpp, speaker.cpp]
2023-08-14 voltage warning through speaker
    because there's no OSD or ELRS telemetry, it has to be done through the beeper
2023-08-21 v0.2 PCB ordered
    [Baro.SchDoc, Connectors.SchDoc, Flash.SchDoc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]
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2023-09-01 moved simulations to "other"
    [INA139.DSN]
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2023-09-03 current sensor (not working)
    [adc.cpp]
2023-09-03 fix blackbox crashing bug
    [blackbox.cpp]
2023-09-03 fix gyro slow
2023-09-04 dshot command doesn't change throttle anymore
2023-09-09 c++ bin to json converter, pin and pid fix
    [blackbox.cpp, pid.cpp, pins.h]
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2023-09-12 configurator stuff, proper air mode
    change over to webserial (temporary until Rust Serialport is fixed)
    [blackbox.cpp, blackbox.h, main.cpp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]
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2023-09-17 fix pids, separate pid gains for each axis
    [blackbox.cpp, pid.cpp]
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2023-10-01 fixed point integer math as class (untested)
    [blackbox.cpp, global.h, pid.cpp]
2023-10-03 remove quaternions/imu
    did not work as expected
    [global.h, main.cpp, pid.cpp]
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2023-10-08 tidy up, speed up (still skipping loop frames)
    [adc.cpp, pid.cpp]
2023-10-08 fix blackbox delete trace
2023-10-09 speed improvements
    still not found the root cause of the peaks, maybe USB interrupts?
2023-12-08 first works on v0.3 pcb
    [Baro.SchDoc, Connectors.SchDoc, Custom Components.PcbLib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]
2023-12-11 PCB v0.3 wip - 0 rule violations, but not happy with routing
    [Baro.SchDoc, Connectors.SchDoc, Custom Components.PcbLib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]
2023-12-13 PCB version 0.3, see Cangelog.md
    [PCB Version 0.3.PrjPcb]
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2023-12-17 switch back to Rust based Serial (somewhat more reliable, real COM ports)
2023-12-17 tidy up pcb, include BOM
    [Main.SchDoc, PCB Version 0.3.xlsx]
2023-12-17 pipe ELRS data through generic UART handler, TinyUSB Stack
2023-12-18 quaternions, but gyro axis still switched and >1ms execution time
2023-12-18 shaved off about 47µs@264MHz during each pid loop
    may go back to original clock speed (132MHz) at some point if I get the cycle time even lower, or something in between
2023-12-18 simplify math
    this way, there is only one quaternion to combine the new gyro value. This makes the order, in which the axis would be applied otherwise, irrelevant. Since this order would just be a definition anywa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
2023-12-22 IMU working, still a few frame drops @1x clock speed
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2024-01-01 removed crashInfo code, because it is unreadable
    [adc.cpp, blackbox.cpp, elrs.cpp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]
2024-01-07 update for V0.3 PCB - not all is working yet
    - SPI code separated from device driver
    - OSD, Gyro and Baro on one SPI, SD on the other
    - SD Blackbox incl. FIFO to Core 0 to deal with saving
    - actual time in BB Log, numerical value
    - removed old Baro code (new code not done yet
    - ELRS on Serial1 now, GPS on Serial2
    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
2024-01-08 Rust style variable types (they're just shorter) :D
    [adc.cpp, baro.cpp, blackbox.cpp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]
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2024-02-02 fixed some program stalls/reboots, task manager, baro to loop1, faster ELRS CRC
    [adc.cpp, baro.cpp, blackbox.cpp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]
2024-02-04 separate barometer read and eval on both cores
    Issues:
    - loop() cannot use spi0, because spi0 is used for the gyro and there are collisions if the spi peripheral was used on both cores
    - loop1() is very time sensitive - it should not do the heavy lifting of floats because if could delay the gyro
    --> solution: read baro on loop1(), then evaluate the data in loop()
    [baro.cpp, main.cpp]
2024-02-04 fix delete the wrong log bug, fix double speaker frequency, ping
    [speaker.cpp]
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2024-02-08 V0.4 PCB
    hopefully fixes all the V0.3 issues:
    - ELRS range --> better grounding, RFX2401C
    - ELRS WiFi --> filter in front of antenna
    - ELRS crystal
    - ELRS boot button
    - I2C Pullups
    - OSD crystal trial and error
    - more spacing for 100nF caps
    [Baro.SchDoc, Connectors.SchDoc, Custom Components.PcbLib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]
2024-02-10 proper altitude estimation using baro, accel and gyro
    No GPS in the equation yet.
2024-02-10 remove GPS from vvel and altitude (for now), bug fixing
    [gps.cpp, pid.cpp]
2024-02-11 improved throttle and altitude logging
    altitude now logged to about 6cm precision, throttle now logged also in altitude hold mode
2024-02-11 fix bugs (RC smoothing, switch to alt hold, initPID)
    - RC smoothing was using a bad sinceLastRCMessage timer (timer was reset before the packet was actually written)
    - starting throttle when switching to alt hold was calculated incorrectly
    - PIDs were only initialized when there was no EEPROM --> values not implemented in EEPROM would not turn to defaults, but would be left at 0 before
    [elrs.cpp]
2024-02-12 sin, cos of fix32 numbers using interpolator
    saves about 6µs (@264MHz) in each PID cycle
2024-02-13 v0.4 as ordered, incl. exports (PDF, Gerber, BOM)
    [PCB Version 0.4.PrjPcb, PCB Version 0.4.xlsx]
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2024-02-19 move solder rig where it belongs
    [Alignment card.prt, Alignment card.stl]
2024-02-20 adjust formatting of code, no content changes
    "C_Cpp.clang_format_fallbackStyle": "{ BasedOnStyle: LLVM, UseTab: ForContinuationAndIndentation, AlignConsecutiveAssignments: true,AlignConsecutiveDeclarations: false, IndentWidth: 4, TabWidth: 4, BreakBeforeBraces: Attach, AllowShortIfStatementsOnASingleLine: true, IndentCaseLabels: false, ColumnLimit: 0, AccessModifierOffset: -4, NamespaceIndentation: All, FixNamespaceComments: false }"
    [adc.cpp, baro.cpp, elrs.cpp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]
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2024-02-23 allow more gyro noise during calibration
    Even slight winds were enough to cancel calibration
2024-02-23 fix some altitude hold stuff
    [pid.cpp]
2024-02-26 WAV file support from SD cards for the speaker/beeper (#1)
    - Sound quality leaves to be desired due to the speaker (beeper). Attaching a decent speaker actually yields decent results
    - Works best with high pitch sounds, speech basically unintelligible
    - start.wav for a boot sound, and some error messages when trying to arm unsafely (throttle up, configurator, ...)
    - fetches 1KiB of data from the SD card each time, then pushes that into one of two buffers that are automatically fed into the PIO using the DMA controller. Requires .wav files with 8 bit PCM and 44.1kHz
    - speaker is in PWM mode per default, only switches to wav mode, when a file is playing. Switches back to PWM afterwards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
    [adc.cpp, blackbox.h, global.h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]
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2024-02-27 working now, still too slow despite reduced oversampling
    [main.cpp, pid.cpp]
2024-02-28 scrap concept: use one pio per motor, including edge detection
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2024-03-08 Update voltage divider for power mux
    fixes 3.3V voltage drops due to the power switch switching too late after removing battery / too early when attaching battery
    [Voltage Regulators.SchDoc]
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2024-03-12 add standalone ELRS RX (as ordered)
    [Custom Components.PcbLib, Custom Components.SchLib, ELRS Logic.SchDoc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]
2024-03-12 (untested) fix of axis
    [pid.cpp]
2024-03-12 limit i term and throttle to 50-2000 in altitude hold mode
    this prevents over/underflow of the throttle
    [pid.cpp]
2024-03-14 actions on connect
    - automatic listing of blackbox files
    - automatic PID gain loading
    - automatic disconnect on page reload
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2024-03-15 use new accel based vvel for vvel, save accel calibration
2024-03-18 fix GPS blackbox recording always on
    [blackbox.h]
2024-03-18 prevent overflow on vertical accel
    [blackbox.cpp]
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2024-03-21 go back to normal accel sampling, imuData -> gyroData
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2024-03-21 buffered blackbox logging
    buffer frames until they can be written, necessary for low BB frequency dividers while using a high amount of flags
2024-03-23 Fix D Term
    The D term was inverted the whole time. No idea how I did not notice this till now, but I guess better late than never
    [pid.cpp]
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2024-03-23 smoothChannels more jitter resistant
    - smoothChannels converted to fix32 -> smoother FF during slow changes
    - smoothing now over a period of 2 RC packets -> more resistant to packet time jitter (both FC and ELRS side)
    [elrs.cpp, pid.cpp]
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2024-03-23 test faster binomial filter
    to be tested next time when flying
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2024-03-29 fix when both touches want to grab the same frame
2024-03-29 add frame number, remove dots with no selected flag
2024-03-29 fix one-off-errors when wheeling
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2024-04-03 tidy up elrs rx
    [ELRS Logic.SchDoc, ELRS_RX_TD_PA_v0.1.PrjPcb]
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2024-04-15 bb flag modifier refactoring, filter recalculation only when filter changes
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2024-04-15 fix mouseMove edge case
2024-04-17 remove ESC selection option, consistent report of motor count
2024-05-29 4way in normal MSP functions
    still some error messages from BlHeliSuite32, but they go away after the second Read Setup
    [4way.cpp, global.h, main.cpp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]
2024-05-30 fix serial function deallocation
    [blackbox.h]
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2024-06-02 Select a custom MSP API version
    the old one was set to avoid conflicts with BlHeli32Suite (lower values required the MSP_IDENT command to be supported, because despite the different firmware identifier, blheli32suite thought in betaflight API versions). The new API version is now separate from other firwares and can be incremented independently
    [msp.h]
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2024-06-02 apply new formatting
    better for git, no longer changes irrelevant lines
    [4way.cpp, adc.cpp, baro.cpp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]
2024-06-06 finished completion and unit tests of fix32/64
    Steps remaining: check all code that uses fix32/fix64 variables, because the interface of some functions was changed. Most notably, multiply64 vs operator*
    [blackbox.cpp, elrs.cpp, msp.cpp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]
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2024-06-08 convert roll pitch yaw to fix32
    [blackbox.cpp, elrs.cpp, msp.cpp]
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2024-12-06 idle throttle scaling, 1024 throttle pipeline
    throttle pipeline was changed from 1000...2000 to 988...2012, allowing less aliasing when converting values
2024-12-06 potential fix for GPS hold
    [pid.cpp]
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2024-12-14 new dshot pio working
    shaves off 11µs of execution time in pid.cpp (35 ms per second, or around 3.5% more free time on the processor)
2024-12-14 use DShot 600, to reduce errors
    if the return packet did not arrive by the time the new packet is being processed (can happen due to jitter in the processing time), then an error is recorded. Faster DShot packets mean the chance is higher that the RPMs have been returned. Down from one error every ~900 frames to 0 errors
2024-12-14 fix ELRS 50 and 250mW power mixed up
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2025-01-16 fix gyro initialization
2025-03-23 Update to Svelte 5 (#53)
    This is more like a dump of the merge, rather than actually merging. I spent a day on this update and in case it becomes useful again, it's nice to have it in the history. Also some of the code is a bit cleaner than before (e.g. fewer circular effects that only stop because of some of the code is asynchronous and therefore untracked by svelte 5 (svelte 4 resolved these circular dependencies!). Third reason: This is the base I used to upgrade to Vue as the frontend framework, which is going great. The next merge will be the conversion to vue (which is somehow easier than migrating from svelte 4 to 5, despite the migration script).
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2025-03-27 PCB version 0.5 (#56)
    See the linked issue or Changelog.md for details
    [ADC.kicad_sch, BOM v0.5 pre.csv, BOM v0.5.csv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]
2025-04-14 RP2350, hVel estimate and more
    some of these features were previously pushed to main already but idk which...
    - RP2350 and PCB v0.5 support (dropped v0.4 support already)
    - horizontal velocity estimate: integrate accel data onto GPS velocity to better interpolate the value -> delay reduced by roughly 200-300 ms on Walksnail M10
    - timezone support in logs
    - increase throttle when tilting in altitude hold, in addition to PID controller
    - position lock in GPS_VEL
    - graph drawing fixes in blackbox viewer, and some other minor configurator fixes
    - better log export (no need to reload from FC - exports the currently open log now)
    - fix ringbuffer copyToArray (corrupted GPS data)
    - automatic lat an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
    [4way.cpp, baro.cpp, blackbox.cpp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]
2025-04-14 Fix WAV file playback (#69)
    - Can play WAV files again
    - PWM instead of PIO => proper high and low level support (greater amplitude) and lower PIO usage
    [global.h, speaker.cpp]
2025-05-18 More settings in configurator, faster Blackbox and more (#72)
    features:
    - implements #73: TCP in configurator
    - CLI tab for quicker prototyping with command history (works through MSP!)
    - Sensors tab (drawing in a different thread)
    - MASSIVE blackbox viewer speed improvements
    - barometer blackbox logging
    - self-hosted font awesome
    - rate visualiser
    - gyro data filtering, anti gravity (PID boost), better FF filtering and I term relax
    fixes:
    - fix repeated Serial messages on linux
    - Fix gyro DMA issues
    - fix atan2 argument order
    - fix mag rear/front
    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
    [adc.cpp, baro.cpp, blackbox.cpp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]
2025-05-18 remove V2 over V1 jumbo, fix jumbo
    [blackbox.cpp, elrs.cpp, msp.cpp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]
2025-06-19 save blackbox view (#79)
    When exiting the blackbox, save the current view and recover it when going back to the blackbox tab
2025-07-02 Longer blackbox file names (#80)
    * fix fat32 timestamp (local timezone instead of UTC)
    * 4 digit blackbox file names, and the blackbox now uses the highest number already present rather than the first free one
    [blackbox.cpp, blackbox.h, msp.cpp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]
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2025-07-05 Different Blackbox frame types (#84)
    Instead of constant width frames, there are now different frame types available:
    - regular frame for e.g. setpoints, PID and motor outputs
    - highlight frame: add bookmarks at the push of a button on the remote
    - flight mode: no longer a blackbox flag, will always be saved and only when it changes
    - ELRS: only when it changes -> reduces space and means lower required bandwidth
    - GPS: only when a new packet arrives (and ALWAYS when a new packet arrives). No longer skipped GPS frames, no more wasted space, no more separated GPS frames over several blackbox frames
    [blackbox.cpp, blackbox.h, global.h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]
2025-07-07 Blackbox improvements (#89)
    - magic number and header reordering
    - blackbox flag reordering
    - rewrote docs for blackbox logging format
    - improved drawing speed of filtered data
    - implemented adjustable stroke width
